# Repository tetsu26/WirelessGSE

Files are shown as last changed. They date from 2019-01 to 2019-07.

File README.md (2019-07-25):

# GSE Ver.2 の解説
東北大学FROM THE EARTH用のGSE制御システムVer.2の解説です．    
質問等は tetsushi_m[at]outlook.jp まで．

# はじめに
FTEのGSEを無線化した経緯について書いておきます．

時は遡ること2017年，この年の能代で突然，点火点と射点の位置が20mくらい伸びたため，今まで使っていたGSEのケーブルの長さが足りなくなってしまったのです．そこで燃焼班の皆様はLANケーブルを調達し，なんか頑張ってどうにかなった（詳しくはよく知らん）のですが，そのときの燃焼班のケーブル半田付けなどがまぁそれはそれは残念だったので，電子班でどうにかしようということになりました．んで，当時流行だった無線GSEに憧れた7期はどうせならFTEのGSEも無線化しちまおうとなったわけです．自然な流れですね．そして当時電子班班長だった私は電子班の誰かに無線GSE開発を押しつけようと声をかけ続けた訳ですが，何かと理由をつけて全員に断られてしまったので仕方なく自分でやることにしたわけです．

そうして無線GSEを作ることになってしまった私ですが，当初はロケットの電装に比べれば，スイッチの状態を送信するだけなんで簡単だろうと高をくくっていた訳です．まぁ"スイッチの状態を送るだけなら"実際簡単な訳ですが．実際作ってみるといろいろな障壁がありました．
* 送信レートの問題
  
  IM920で使ってる920MHz帯は送信時間の制限が厳しくて，データを連続送信できないため，5Hz位でしかスイッチの状態を反映できない．
* IM920 の通信距離
  
  7km飛ぶとかいっときながら見通しでも300m位しか通信できない．ちょっと怖い．
* 打ち上げシーケンス中に通信途切れた時の対処
  
  ダンプするしかない．悲しい．
* 卍伊豆大島卍
  
  活火山なだけあって何かが島から出ている．無線が飛ばない．見通しで100mがやっと．
* 責任
  
  無線GSEがしくじるとロケットが飛ばない訳でみんなの努力が報われない．打ち上げ前は気が気じゃない．
  
そのたもろもろ．思ったより大変だった．

そんなこんなで無線GSEを作っていると思うわけです．点火点と射点，ケーブルでつなげばよくね？　俗に言う原点回帰って奴です．有線なら通信の安定性とか考えなくていいし，ケーブルの断線だけ気をつけていればいいよね．そこで電子班何人かで有線GSEを総点検し，やばそうな半田付けは直し，ケーブルも完璧に作り直しました．

つまり，このくそ長いはじめにで何が言いたいかというと，**「無線使うな有線を使え」** ということです．きっとこれを読んでいるあなたは不幸にも無線GSEを押しつけられてしまったしがない電子班員でしょう．ご愁傷さま．燃焼班員にあったら是非伝えてください． **「無線使うな有線を使え」** と．あいつらはこの無線GSEのやばさを知りません．健闘を祈ります．

# よく燃焼班に聞かれること・注意すべきこと
* 無線のチャンネルは？  
  プログラムコードからは変更できない．IM920の設定から変更する．ググれば出てくるし，[この辺のサイト](https://www.interplan.co.jp/solution/wireless/im920/im920.php)を参考にすべし．

* 安全対策は？  
  万が一Fill中に通信が途絶えてもFillが止まるように，Fillには時間制限がかかっている．時間制限はロケット側のGSEのプログラムを書き換えることで変更できる．デフォルトでは60秒以上Fillが続くと強制的に30秒ダンプする．  
  同様に，Oxyも60秒以上入らないようになっている．このときはダンプせず，システムを再起動する．

# 使っている主な部品  
* マイコン    MBED LPC1768  
まぁいつもの．ピンがいっぱいあるから．
* 3端子dcdc   BP5293-50   http://akizukidenshi.com/catalog/g/gM-11188/  
3端子レギュレーターは効率悪いし，村田のdcdcコンバータは半田付けが難しすぎるので．  
ざっと計算した感じ，1Aもあれば，IM920含めて余裕で足りる．
* リレー    946H-1C-5D  http://akizukidenshi.com/catalog/g/gP-07342/  
mbedのdigital out は40mAまでしか出せないので，リレーは動かせなさそうだった．  
5Vのリレーをトランジスタでスイッチングするのがいいと思った．   
* 無線モジュール    IM920  
協賛でもらったやつ．正直無線GSEには向いてない．

# プログラムコード
\SourceCode にあります．mbedオンラインコンパイラにコピペして使ってください．
ロケット側と点火点側でソースコードが分かれてるんで気をつけてください．

## コード解説_点火点側
ソースコードはc++(ほぼC)で書いてあります．一応頭から説明しておきます．

```cpp
#include<mbed.h>
#include<IM920.h>
#include<cstring>
```
ライブラリのインポートです（それはそう）．

```cpp
#define IM920_TX p13
#define IM920_RX p14
#define IM920_BUSY p11
#define IM920_RESET p12
#define IM920_SERIAL_BANDRATE 19200//im920の通信レート
```
IM920関係のピン設定ですね．

```cpp
DigitalOut myled(LED1);
DigitalOut myled2(LED2);
DigitalOut myled3(LED3);
DigitalOut myled4(LED4);
DigitalOut led_fill(p16);
DigitalOut led_dump(p18);
DigitalOut led_oxy(p20);
DigitalOut led_fire(p21);
DigitalOut led_1(p24);
DigitalOut led_2(p23);
PwmOut buzzer(p26);

DigitalIn fill(p15);
DigitalIn dump(p17);
DigitalIn oxy(p19);
DigitalIn fire(p22);

IM920 im920(p13, p14, p11, p12,19200);//無線通信用のserialクラス
Serial pc(USBTX, USBRX);
```
そのたもろもろのピン設定です．基板自作したときは適宜変えてください．

```cpp
// グローバルな奴ら
char send_data[8];    //送信するデータを格納する変数
char recv_data[8];    //受信すry)
int cb_count = 0;     //割り込み回数を数えるやつ
int i = 0;            //一秒間隔で赤いLEDを点滅させるのに使う
```
グローバル変数です．

```cpp
int fire_buzzer(int i)
{
    if(i == 1)
    {
        buzzer.period(1.0/440.0);  //多分"ラ"
        buzzer.write(0.5f);
        wait(0.5f);
        buzzer.write(0.0f);
    }
    
    return 0;
}
```
これは fire をオンにしたときにブザーから音を出すための関数です．音程が気に入らない人は変えてください．

### callback() 関数

```cpp
void callback () {  //受信時の割り込み関数（受信したときに送信するコード）
    int i;

    cb_count++; //割り込みの回数を数える変数
    
    i = im920.recv(recv_data, 8);
    recv_data[i] = 0;
    pc.printf("recv: '%s' (%d)\r\n", recv_data, i);
    
    if (recv_data[0] == '5' || recv_data[7] == '5')     //きちんとデータを受け取れたか確認
    {
        led_fill = recv_data[1] - '0';           
        led_dump = recv_data[2] - '0';
        led_oxy = recv_data[3] - '0';
        led_fire = recv_data[4] - '0';
        fire_buzzer(led_fire);
    }
    //8文字1セットで送ることにする
    send_data[0] = '5';   //データ始まりの合図
    send_data[1] = '0'+(fill.read()^ 1);      //プルアップしてるからHiとLoを反転
    send_data[2] = '0'+(dump.read()^ 1);
    send_data[3] = '0'+(oxy.read()^ 1);
    send_data[4] = '0'+(fire.read()^ 1);
    // 5~6はとりあえず未使用
    send_data[5] = '0';
    send_data[6] = '0';
    send_data[7] = '5';   //データ終わりの合図
        
    im920.sendData(send_data,8);    //8文字送りますよーってやつ
    //pc.printf("send:%s\r\n cb_count:%d\r\n",send_data,cb_count);

}
```
これはim920が受信したときに実行される予定の関数です．グローバル関数にiがあるのにローカルでもiを宣言して使うくそコードになってますね，今気づきました．ここからわかりにくいと思うので詳しく書いておきます．
```cpp
i = im920.recv(recv_data, 8);
recv_data[i] = 0;
pc.printf("recv: '%s' (%d)\r\n", recv_data, i);
```
この辺はおまじないです．書いておいてください．
```cpp
if (recv_data[0] == '5' || recv_data[7] == '5')     //きちんとデータを受け取れたか確認
    {
        led_fill = recv_data[1] - '0';           
        led_dump = recv_data[2] - '0';
        led_oxy = recv_data[3] - '0';
        led_fire = recv_data[4] - '0';
        fire_buzzer(led_fire);
    }
```
これは効果あるかは謎ですが，受信したデータの整合性を確認しているつもりです．受信データ（8桁）の最初と最後の数字は`5`なのでそれだけ確認しています．

その後の`led_fill = recv_data[1] - '0';`ですが，これは受信した8桁の2文字目がfillの状態を示しているのでそれをスイッチについたLEDに反映しています．受信したデータは`recv_data`に格納されているのですが，ASCIIコードなので`0`のASCIIコードを引くことで元の送信した数字に戻しています．ほかも同じです．
```cpp
 //8文字1セットで送ることにする
    send_data[0] = '5';   //データ始まりの合図
    send_data[1] = '0'+(fill.read()^ 1);      //プルアップしてるからHiとLoを反転
    send_data[2] = '0'+(dump.read()^ 1);
    send_data[3] = '0'+(oxy.read()^ 1);
    send_data[4] = '0'+(fire.read()^ 1);
    // 5~6はとりあえず未使用
    send_data[5] = '0';
    send_data[6] = '0';
    send_data[7] = '5';   //データ終わりの合図
```
この辺はスイッチの状態を読み取って送信するデータを作っています．`send_data`配列の５と６は将来のために未使用です．送る文字数を８文字にしたのはなんとなくきりがいいからです．
```cpp
im920.sendData(send_data,8);    //8文字送りますよーってやつ
```
そしてここで上で作った文字列を送信しています．

### callback2() 関数
```cpp
void callback2()    //受信割り込みの回数を数える関数
{
    
    if(cb_count == 0)
    {
        pc.printf("yabame\r\n");
        NVIC_SystemReset();         //一秒間に一回も通信しなかったらリセットする
        
    }
    else
    {
        cb_count = 0;
        if(i == 0)
        {
            led_2 = 1;
            i++;
        }else{
            led_2 = 0;
            i = 0;
        }

    }
}
```
これは接続が切れたときの対処です．コードをざっくり見てもらうと気づくと思うのですが，このコードには「受信したら割り込み処理で送信する」機能しかないので，一度接続が切れる（というかデータのやりとりが途絶える）と復帰できなくなる問題があります．なので`callback2()`関数を1秒ごとに起動してもしその前1秒間に一度も通信していなかったらこのmbedをリセットして`main()`関数をもう一度頭から実行します．`NVIC_SystemReset()`ってのはmbedのリセットボタンを押した状態をコードから作れる魔法の言葉です．

### main()関数
```cpp
int main()
{
    //各スイッチをプルアップする
    fill.mode(PullUp);
    dump.mode(PullUp);
    oxy.mode(PullUp);
    fire.mode(PullUp);          

    im920.init();
    //Im920受信の割り込みを設定
    im920.attach(callback);
    pc.baud(115200);
    pc.printf("Wireless GSE controll system started!!\r\n");
    
    Ticker timeout;
    timeout.attach(&callback2,1);
    
    myled = 1;  //設定完了の合図
    led_1 = 1; 
    im920.poll();
    im920.sendData(send_data,8);    
    
    while(1){   
        im920.poll();//双方向送受信に必要らしい
       // wait_ms(1);  //意味なさそうだけどあると安定する
        
    }
    
}
```
ここは特に説明することもない気がします．セットアップの時に1度データを送信します．

## コード解説_ロケット側
同じように解説書いておきます．
```cpp
#include<mbed.h>
#include<IM920.h>

#define IM920_TX p13
#define IM920_RX p14
#define IM920_BUSY p11
#define IM920_RESET p12
#define IM920_SERIAL_BANDRATE 19200//im920の通信レート

//LED&SWITCHたち      
DigitalOut myled(LED1);
DigitalOut myled2(LED2);
DigitalOut myled3(LED3);
DigitalOut myled4(LED4);
DigitalOut fill(p21);
DigitalOut dump(p22);
DigitalOut oxy(p23);
DigitalOut fire(p24);

IM920 im920(p13, p14, p11, p12,19200);//無線通信用のserialクラス
Serial pc(USBTX, USBRX);
```
まぁこの辺は説明するまでもないでしょ．
```cpp
char send_data[8];    //送信するデータを格納する変数
char recv_data[8];    //受信すry)
int fill_count = 0;     //fillの割り込みの回数を数えるやつ
int oxy_count = 0;     //oxyの割り込みの回数を数えるやつ
```
グローバル変数の定義．

### callback()関数
```cpp
void callback () {
    int i;
    int fire_count = 0;
    
    i = im920.recv(recv_data, 8);
    recv_data[i] = 0;
    printf("recv: '%s' (%d)\r\n", recv_data, i);
    
    if (recv_data[0] == '5' || recv_data[7] == '5')     //きちんとデータを受け取れたか確認
    {
        fill = recv_data[1] - '0';           
        dump = recv_data[2] - '0';
        oxy = recv_data[3] - '0';
        fire_count = recv_data[4] - '0';
        
        if(fire_count == 1 && oxy == 1){
            fire = 1;
        }else{
            fire = 0;
        }
        
    }
    /*
    for(int i = 0; i < 8; i++)
    {
        send_data[i] = recv_data[i];
    }
    */
    im920.sendData(recv_data,8);
    //printf("send!!:%s\r\n",recv_data);
}
```
点火点側の`callback`関数とほとんど同じです．ただ，`oxy`が入ってないと`fire`がオンにならないようにしてあります．

### fillcount()関数
```cpp
void fillcount()    //受信割り込みの回数を数える関数
{
    if(fill == 1)
    {
        fill_count += 1;
    }else{
        fill_count = 0;
    }
    
    if(oxy == 1)
    {
        oxy_count += 1;
    }else{
        oxy_count = 0;
    }
    
    printf("fill_count: %d\r\n",fill_count);
    printf("oxy_count: %d\r\n",oxy_count);
    if(fill_count >= 60)
    {
        fill = 0;
        dump = 1;
        printf("recovery mode!!! Dump 30second\r\n");
        wait(30);
        printf("reboot!!");
        NVIC_SystemReset(); 
        
    }
    if(oxy_count >= 60)
    {
        oxy = 0;
        printf("recovery mode!!!\r\n");
        printf("reboot!!");
        NVIC_SystemReset(); 
    }
    
}
```
この関数を1秒に一回割り込みさせることで，`fill`がオンになってる秒数などを数えています．
```cpp 
if(fill_count >= 60)
```
の60をいじるとFill時間に制限をかけられます．60の時は一分以上はFillできないという具合です．

### main()関数
```cpp
int main()
{
    
    pc.baud(115200);
    pc.printf("*** IM920\r\n");
    
    /* 受信側との接続を確立する */
    
    im920.init();

    im920.attach(callback);
    myled = 1;          //設定完了の合図
    
    Ticker fill_limit;
    fill_limit.attach(&fillcount,1);
    
    im920.poll();

    while(1){
       im920.poll();
       //wait_ms(1);
    }
    
}
```
特にいうことはないです．
```cpp
    Ticker fill_limit;
    fill_limit.attach(&fillcount,1);
```
でfillcount関数に1秒おきの割り込みを設定しています．

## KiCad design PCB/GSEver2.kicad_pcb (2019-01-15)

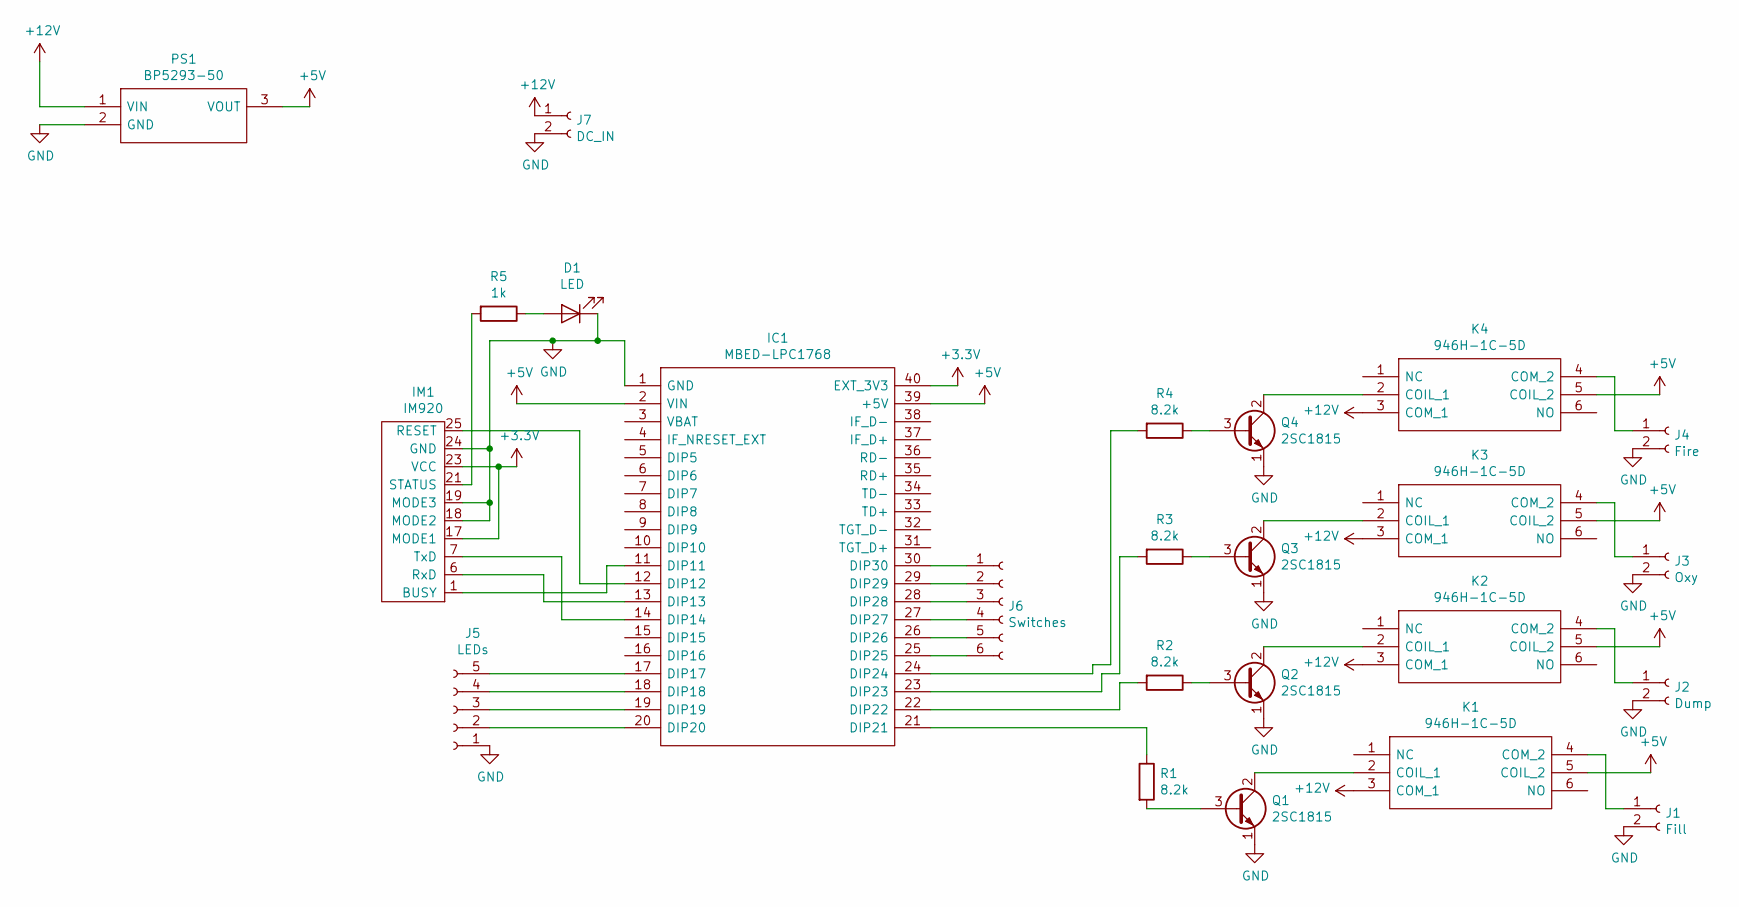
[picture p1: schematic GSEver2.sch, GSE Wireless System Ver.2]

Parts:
D1: LED; LED_D3.0mm
IC1: MBED-LPC1768; DIPS2286W63P254L5370H300Q40N; Manufacturer_Part_Number MBED-LPC1768
IM1: IM920
J1: Fill; JST_XH_B02B-XH-A_02x2.50mm_Straight
J2: Dump; JST_XH_B02B-XH-A_02x2.50mm_Straight
J3: Oxy; JST_XH_B02B-XH-A_02x2.50mm_Straight
J4: Fire; JST_XH_B02B-XH-A_02x2.50mm_Straight
J5: LEDs; JST_XH_B05B-XH-A_05x2.50mm_Straight
J6: Switches; JST_XH_B06B-XH-A_06x2.50mm_Straight
J7: DC_IN; JST_XH_B02B-XH-A_02x2.50mm_Straight
K1, K2, K3, K4: 946H-1C-5D; 946H1C5D; Manufacturer_Part_Number 946H-1C-5D
PS1: BP5293-50; TO254P570X1690X1800-3P; Manufacturer_Part_Number BP5293-50
Q1, Q2, Q3, Q4: 2SC1815; TO-92_Inline
R1, R2, R3, R4: 8.2k; R_Axial_DIN0207_L6.3mm_D2.5mm_P10.16mm_Horizontal
R5: 1k; R_Axial_DIN0207_L6.3mm_D2.5mm_P10.16mm_Horizontal

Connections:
+3V3: IC1.40 (EXT_3V3), IM1.17 (MODE1), IM1.23 (VCC); also elsewhere on the board
+5V: IC1.2 (VIN), IC1.39 (+5V), K1.5 (COIL_2), K2.5 (COIL_2), K3.5 (COIL_2), K4.5 (COIL_2), PS1.3 (VOUT); also elsewhere on the board
+12V: J7.1, K1.3 (COM_1), K2.3 (COM_1), K3.3 (COM_1), K4.3 (COM_1), PS1.1 (VIN)
GND: D1.1 (K), IC1.1 (GND), IM1.18 (MODE2), IM1.19 (MODE3), IM1.24 (GND), J1.2, J2.2, J3.2, J4.2, J5.1, J7.2, PS1.2 (GND), Q1.1 (E), Q2.1 (E), Q3.1 (E), Q4.1 (E); also elsewhere on the board
unnamed: D1.2 (A), R5.1
unnamed 13: IC1.11 (DIP11), IM1.1 (BUSY); also elsewhere on the board
unnamed 14: IC1.12 (DIP12), IM1.25 (RESET); also elsewhere on the board
unnamed 15: IC1.13 (DIP13), IM1.6 (RxD); also elsewhere on the board
unnamed 16: IC1.14 (DIP14), IM1.7 (TxD); also elsewhere on the board
unnamed 19: IC1.17 (DIP17), J5.5; also elsewhere on the board
unnamed 20: IC1.18 (DIP18), J5.4; also elsewhere on the board
unnamed 21: IC1.19 (DIP19), J5.3; also elsewhere on the board
unnamed 22: IC1.20 (DIP20), J5.2; also elsewhere on the board
unnamed 23: IC1.21 (DIP21), R1.1; also elsewhere on the board
unnamed 24: IC1.22 (DIP22), R2.2; also elsewhere on the board
unnamed 25: IC1.23 (DIP23), R3.2; also elsewhere on the board
unnamed 26: IC1.24 (DIP24), R4.2; also elsewhere on the board
unnamed 27: IC1.25 (DIP25), J6.6; also elsewhere on the board
unnamed 28: IC1.26 (DIP26), J6.5; also elsewhere on the board
unnamed 29: IC1.27 (DIP27), J6.4; also elsewhere on the board
unnamed 30: IC1.28 (DIP28), J6.3; also elsewhere on the board
unnamed 31: IC1.29 (DIP29), J6.2; also elsewhere on the board
unnamed 32: IC1.30 (DIP30), J6.1; also elsewhere on the board
unnamed: IM1.21 (STATUS), R5.2
unnamed: J1.1, K1.4 (COM_2)
unnamed: J2.1, K2.4 (COM_2)
unnamed: J3.1, K3.4 (COM_2)
unnamed: J4.1, K4.4 (COM_2)
unnamed: K1.2 (COIL_1), Q1.2 (C)
unnamed: K2.2 (COIL_1), Q2.2 (C)
unnamed: K3.2 (COIL_1), Q3.2 (C)
unnamed: K4.2 (COIL_1), Q4.2 (C)
unnamed: Q1.3 (B), R1.2
unnamed: Q2.3 (B), R2.1
unnamed: Q3.3 (B), R3.1
unnamed: Q4.3 (B), R4.1

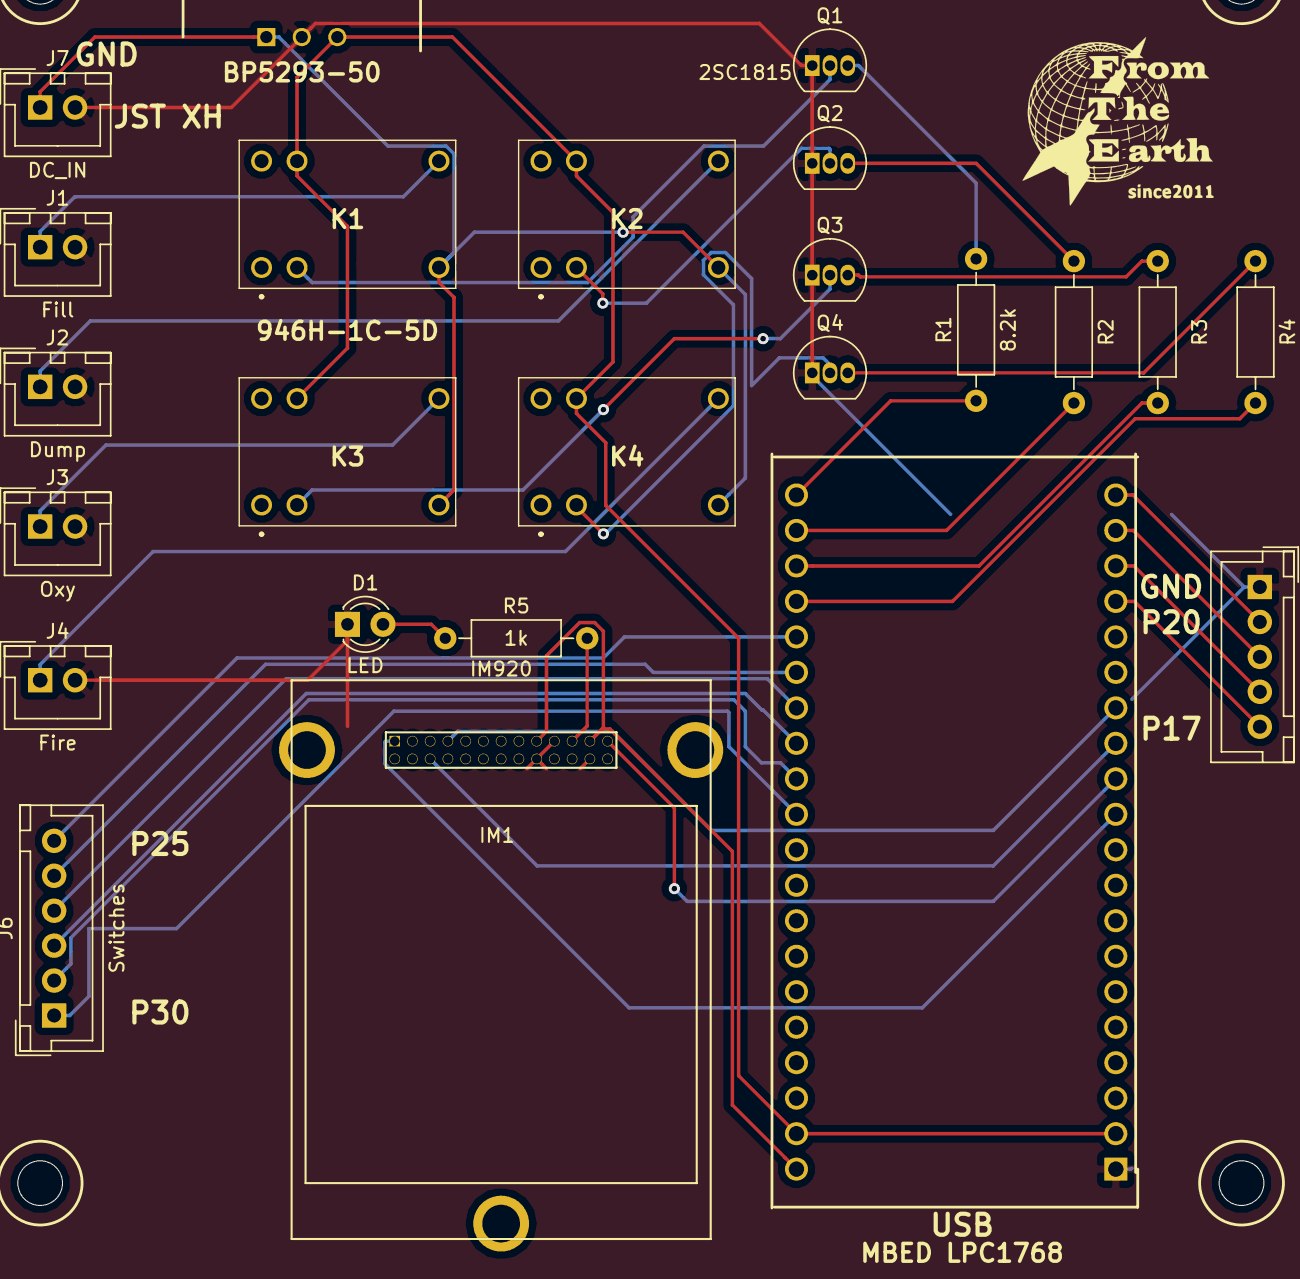
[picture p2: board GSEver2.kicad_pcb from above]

Board: 2 copper layers, 25 parts (0 on the bottom side), 36 nets.

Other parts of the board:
LEDs: LEDs; JST_XH_B05B-XH-A_05x2.50mm_Straight
M3: MountingHole_3.2mm_M3_ISO14580
MBED LPC1768: MBED-LPC1768; DIPS2286W63P254L5370H300Q40N

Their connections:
+3V3: MBED LPC1768.40; also elsewhere on the board
+5V: MBED LPC1768.2, MBED LPC1768.39; also elsewhere on the board
GND: LEDs.1, MBED LPC1768.1; also elsewhere on the board
unnamed 13: MBED LPC1768.11; also elsewhere on the board
unnamed 14: MBED LPC1768.12; also elsewhere on the board
unnamed 15: MBED LPC1768.13; also elsewhere on the board
unnamed 16: MBED LPC1768.14; also elsewhere on the board
unnamed 19: LEDs.5, MBED LPC1768.17; also elsewhere on the board
unnamed 20: LEDs.4, MBED LPC1768.18; also elsewhere on the board
unnamed 21: LEDs.3, MBED LPC1768.19; also elsewhere on the board
unnamed 22: LEDs.2, MBED LPC1768.20; also elsewhere on the board
unnamed 23: MBED LPC1768.21; also elsewhere on the board
unnamed 24: MBED LPC1768.22; also elsewhere on the board
unnamed 25: MBED LPC1768.23; also elsewhere on the board
unnamed 26: MBED LPC1768.24; also elsewhere on the board
unnamed 27: MBED LPC1768.25; also elsewhere on the board
unnamed 28: MBED LPC1768.26; also elsewhere on the board
unnamed 29: MBED LPC1768.27; also elsewhere on the board
unnamed 30: MBED LPC1768.28; also elsewhere on the board
unnamed 31: MBED LPC1768.29; also elsewhere on the board
unnamed 32: MBED LPC1768.30; also elsewhere on the board

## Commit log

2019-06-18 Delete Specification.md
    このファイルいらなくね？
2019-07-03 ソースコードぶち上げた
2019-07-03 Update README.md
    色つけた
2019-07-18 書き足した
2019-07-23 はじめにを書いた
2019-07-25 ロケット側のコード解説も書いた

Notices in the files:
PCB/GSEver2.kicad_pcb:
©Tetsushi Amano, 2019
